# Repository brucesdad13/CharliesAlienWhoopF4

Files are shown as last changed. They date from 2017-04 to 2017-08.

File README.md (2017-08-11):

# UPDATE -- Charlie's AlienWhoop F4 is now OBSOLETE. A new version, deriving from [Lance's AlienFlight F3 Brushed Quad](https://github.com/brucesdad13/AlienFlightArchive/tree/master/Flight-Controllers/F3-V1/F3-Quad), based on the F7 processor has been developed. The AlienWhoop F7 board is backwards compatible, on the same PCB, with F4. The content below has been preserved for historical purposes. Please continue on to [AlienWhoop F7](https://github.com/brucesdad13/AlienWhoopF7)

IMAGE AlienWhoop F4 Flight Controller Welcome

IMAGE AlienWhoop F4 Flight Controller PCB Top Side IMAGE AlienWhoop F4 Flight Controller PCB Bottom Side

# AlienWhoopF4 Features :alien:
AlienFlight F4 remixed for Tiny Whoop/Inductrix

* High-performance ST Microelectronics ARM Cortex-M4 core F4 168 MHz CPU
* Invensense MPU-9250 Nine-Axis (Gyro + Accelerometer + Compass) low power consumption MEMS MotionTracking™ Device
* Latest BetaFlight support (via ALIENFLIGHTF4 target) capable of 32kHz gyro sampling and 16kHz PID loop
* Fairchild Semiconductor FDMA410NZ MOSFET with 9.5A continuous and 24A burst brushed motor insanity (8.5mm coreless scream)

## DIY Flight Controller :alien:
Order your own PCBs from OSH Park by visiting the link below. I recommend ordering the 2oz copper 0.8mm thickness PCB. It takes about three weeks but that will allow plenty of time to order components from the bill of materials in the resources folder. I don't receive any commission or compesation when you order from OSH Park--simply created as a convenience to you (**Note: this version is now obsolete please see the AlienWhoop F7**).
* https://oshpark.com/

## Official Facebook page :alien:
Charlie's AlienWhoop F4 has a Facebook page:
* https://www.facebook.com/alienwhoop/

## See the AlienWhoop F4 in action on YouTube :alien:

IMAGE Soldering the AlienWhoop F4 (https://youtu.be/lKBv_KNc1kM?list=PLFRS68bDc858ymXzT-Lwq0kM343hY3uC5)

IMAGE Charlie's AlienWhoopF4 Takes On Brewmaster's Drone Night 3/25/2017 (https://www.youtube.com/watch?v=Dv2q1gmsQvg)

IMAGE Warm Weather AlienWhoopin' (https://www.youtube.com/watch?v=nY42n2VDJSA)

May this work be of benefit and bring much joy and happiness!

## Acknowledgements :alien:

Deep bows of appreciation and thanks to Lance for his original work and tremendous
generosity in releasing his labor of love for the benefit of all flight controller
enthusiasts. Check out AlienWhoop's heritage at Lance's site:
* http://alienflight.com/ ~ offline as of June 2017
* https://github.com/brucesdad13/AlienFlightArchive ~ Archive of Lance's AlienFlight CC BY-SA suite of flight controllers

Equally deep bows to Jesse Perkins, creator of Tiny Whoop, and the source of inspiration and love for tiny brushed quads.
* http://www.tinywhoop.com/ ~
* https://www.facebook.com/groups/tinywhoop/ ~

Appreciation and respect also goes out to the contributors to the BetaFlight ALIENFLIGHTF4 target including Michael Jakob (MJ666), Martin Budden (martinbudden), and J Blackman (blckmn). Special thanks to Michael Jakob (MJ666) for clearing up confusion on the MPU-9250 magnetometer / compass driver and for updating to MPU-6500 code to work with whichever MPU you decide upon 6500 or 9250 (with compass).

Others deserving thanks for answering questions include in no specific order (and many others):
* OSH Park
* Adam Madron
* Joel Goetze
* Gary Baynes
* Peter (Pedro) Newman

~ Please note: AlienWhoop is not affiliated with nor endorsed by Lance (alienflight.com) or any other Alien projects. The use of Alien in the name and the alien head vector graphic used on the board silkscreen are nods to the lineage of this remix and to the work of Lance and others who created the conditions for this project to arise. Likewise, AlienWhoop is not affiliated with nor endorsed by Tiny Whoop. The Whoop in the name comes from Jesse Perkin's fantastic Tiny Whoop ("a small first-person-view aircraft that truly allows you to feel the gift of flight and the feeling of being tiny" [tinywhoop.com]) and is simply a nod to his efforts and the TW community worldwide.

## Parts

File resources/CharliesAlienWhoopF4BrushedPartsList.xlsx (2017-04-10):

Part | Value | Description | MF | MPN | Mouser | DigiKey | Notes
USB | 10118193-0001LF | Micro-B USB Connector | FCI | 10118193-0001LF | $0.41 |  | Sidemount USB connector
M1 | 53047-0210 | Motor Connector | MOLEX | 53047-0210 | $0.24 |  | Mouser 10 @24 cents
M2 | 53047-0210 | Motor Connector | MOLEX | 53047-0210 | $0.24
M3 | 53047-0210 | Motor Connector | MOLEX | 53047-0210 | $0.24
M4 | 53047-0210 | Motor Connector | MOLEX | 53047-0210 | $0.24
S1 | 2POS-DIP-SWITCH | 2 Position Dip Switch | OMRON | A6H-2102 | $2.55 |  | Substituted for A6H-2101 (backordered)
ACT1 | BLUE | SMD CHIP LED | Kingbright | APHCM2012QBC/D-F01 | $0.21 |  | Mouser 10 @21 cents
ACT2 | BLUE | SMD CHIP LED | Kingbright | APHCM2012QBC/D-F01 | $0.21 |  | IMPORTANT to order BLUE and only BLUE
PWR | BLUE | SMD CHIP LED | Kingbright | APHCM2012QBC/D-F01 | $0.21
R3 | 10K | RESISTORS | Vishay | CRCW060310K0FKEAHP | $0.11 |  | Mouser 10 @11 cents
R4 | 10K | RESISTORS | Vishay | CRCW060310K0FKEAHP | $0.11
R5 | 10K | RESISTORS | Vishay | CRCW060310K0FKEAHP | $0.11
R6 | 10K | RESISTORS | Vishay | CRCW060310K0FKEAHP | $0.11
R7 | 10K | RESISTORS | Vishay | CRCW060310K0FKEAHP | $0.11
R8 | 10K | RESISTORS | Vishay | CRCW060310K0FKEAHP | $0.11
Y1 | 8mhz | SMD Ceramic Resonators | Murata | CSTCE8M00G55-R0 | $0.44
Q1 | FDMA410NZ | N-Channel MOSFET | Fairchild | FDMA410NZ | $0.46 |  | Mouser 10 @46 cents
Q2 | FDMA410NZ | N-Channel MOSFET | Fairchild | FDMA410NZ | $0.46
Q4 | FDMA410NZ | N-Channel MOSFET | Fairchild | FDMA410NZ | $0.46
Q5 | FDMA410NZ | N-Channel MOSFET | Fairchild | FDMA410NZ | $0.46
C4 | 4.7uF | CAPACITORS | Murata | GRJ188C70J475KE11D | $0.16
C7 | 4.7uF | CAPACITORS | Murata | GRJ188C70J475KE11D | $0.16
C10 | .01uF | CAPACITORS | Murata | GRM188R71C103KA01D | $0.03 |  | Mouser 10 @.027 c
C1 | .1uF | CAPACITORS | Murata | GRM188R71C104KA01D | $0.01 |  | Mouser 10 @.01 c
C12 | .1uF | CAPACITORS | Murata | GRM188R71C104KA01D | $0.01
C2 | .1uF | CAPACITORS | Murata | GRM188R71C104KA01D | $0.01
C3 | .1uF | CAPACITORS | Murata | GRM188R71C104KA01D | $0.01
C5 | .1uF | CAPACITORS | Murata | GRM188R71C104KA01D | $0.01
C6 | .1uF | CAPACITORS | Murata | GRM188R71C104KA01D | $0.01
C9 | .1uF | CAPACITORS | Murata | GRM188R71C104KA01D | $0.01
C8 | 1uF | CAPACITORS | Murata | GRM188R71C105KA12D | $0.04 |  | Mouser 10 @.044c
Q3 | IRLML6402 | P-Channel MOSFET | IR | IRLML6402 | $0.38
C11 | 10uF | CAPACITORS | Taiyo Yuden | JMK212AB7106KG-T | $0.22 |  | Mouser 10 @.21c
C13 | 10uF | CAPACITORS | Taiyo Yuden | JMK212AB7106KG-T | $0.22
U1 | MPU9250 | 9-Axis Motion Sensor | Invensense | MPU-9250 |  | $10.64 | Digikey P/N 1428-1019-1-ND
L1 | 2.2uH | 3X3mm Inductor | Taiyo Yuden | NR3015T2R2M | $0.23 |  | Mouser 10 @.23c
MCU | STM32F405RGT | STM32F405RGT | ST | STM32F405RGT |  | $10.58 | Digikey P/N 497-11767-ND
U2 | TPS63001 | Buck/Boost Converter | TI | TPS63001DRCR | $2.25 |  | Mouser 10 @2.02
BAT | JST-PH2.0-PIGTAIL | PowerWhoop Pigtail connector | RDQ | N/A |  | $2.00 | $2 at RaceDayQuads http://bit.ly/2mS2jrU
PCB | PCB | Blade Inductrix shaped PCB | OSH Park | 2oz 0.8mm (http://docs.oshpark.com/services/two-layer-hhdc/) |  | $6.50 | $6.50 for 3 PCB minimum order
RX | LemonRX | LemonRX DSM2 receiver | Lemon | LM0001 (http://www.lemon-rx.com/index.php?route=product/product&path=59&product_id=98) |  | $7.80 | Price seems to have gone up $2.80
Subtotals |  |  |  |  | $11.24 | $37.52
Grand total |  |  |  |  |  | $48.76 | plus shipping the various components
* Recommend directly solder LemonRX. Place face down on bottom side of FC. No JST-ZR_3-PIN connector needed
** Recommend using JST 2.0 pigtail with matching 1S LiPOs >= 200mAh
*** AlienFlight F4 remixed for Tiny Whoop/Inductrix license CC BY-NC-SA 4.0
Optional classic AlienFlight parts: |  |  |  |  |  | DigiKey
REC | JST-ZR_3-PIN | 3 Pin Receiver | JST | S3B-ZR |  | $0.66 | Digikey P/N 455-1694-1-ND
BATT | 3.7V | Battery Connector | JST | S2B-PH-K-S |  | $0.17

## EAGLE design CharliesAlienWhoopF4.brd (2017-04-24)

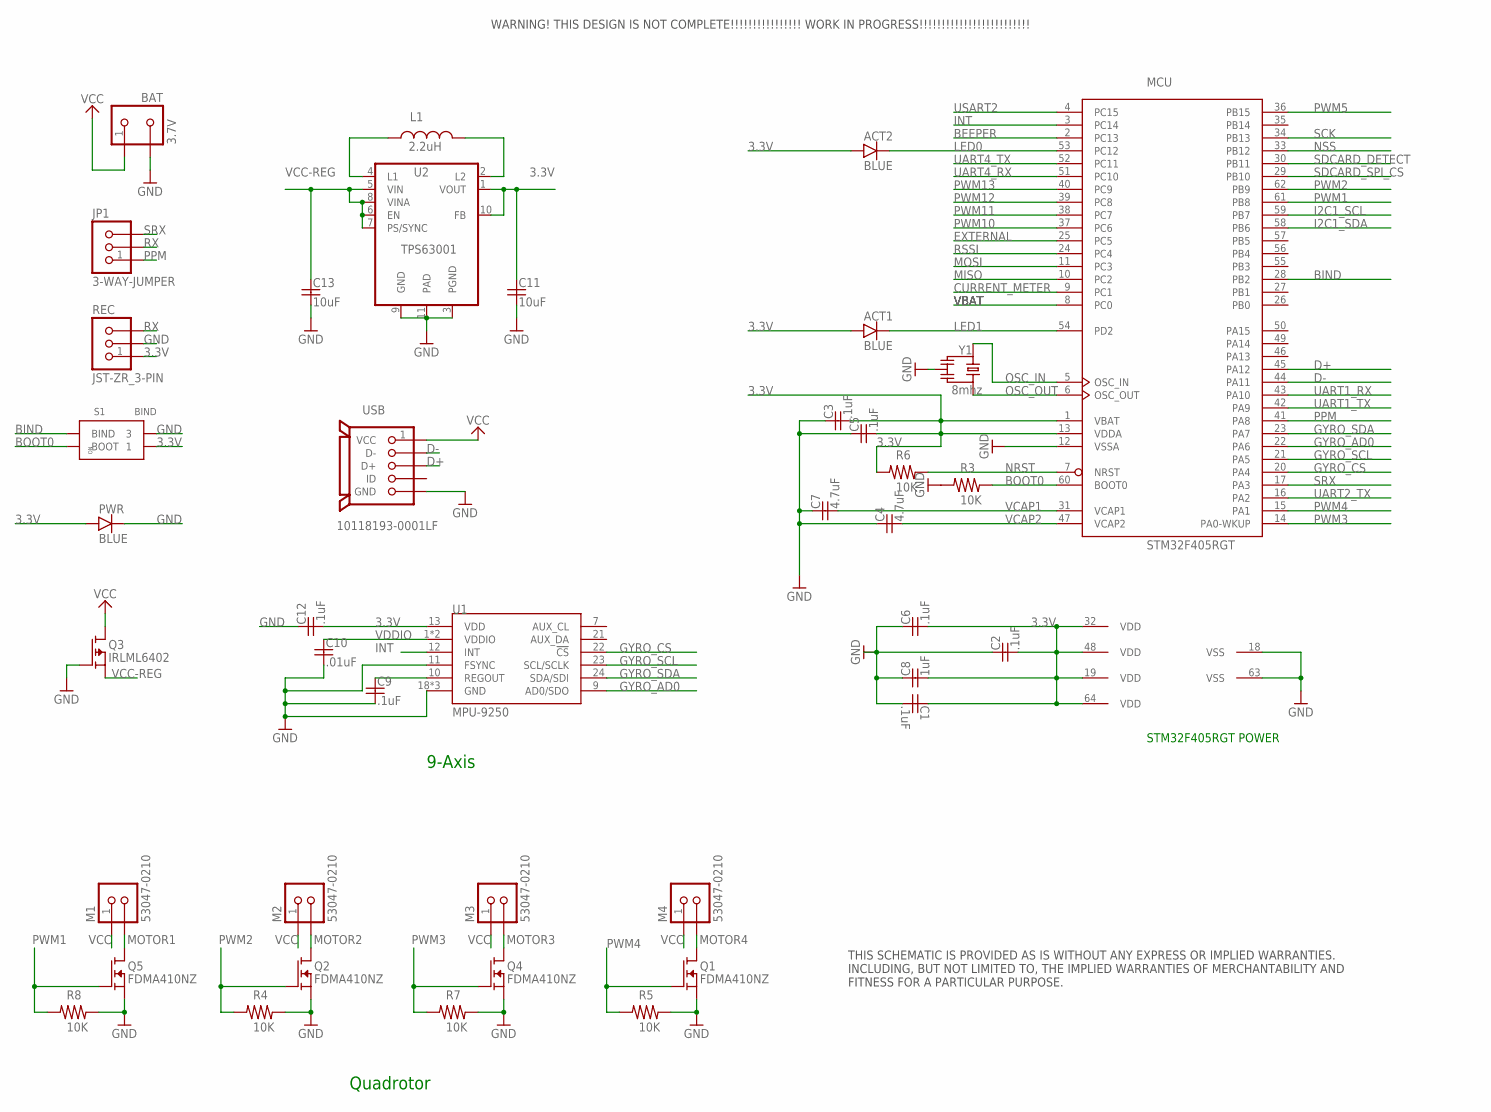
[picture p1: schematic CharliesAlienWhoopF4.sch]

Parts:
ACT1, ACT2: BLUE; SMD-CHIP-LED-0805
BAT: 3.7V; S2B-PH-K-S
C1, C2, C3, C5, C6, C9, C12: .1uF; MUR-CAP-0603
C4, C7: 4.7uF; MUR-CAP-0603
C8: 1uF; MUR-CAP-0603
C10: .01uF; MUR-CAP-0603
C11, C13: 10uF; YUDEN-CAP-0805
JP1: 3-WAY-JUMPER
L1: 2.2uH; NR301X
M1, M2, M3, M4: 53047-0210; PICO-53047-02
MCU: STM32F405RGT; LQFP64
PWR: BLUE; SMD-CHIP-LED-0805
Q1, Q2, Q4, Q5: FDMA410NZ; MICROFET-2X2
Q3: IRLML6402; SOT-23
R3, R4, R5, R6, R7, R8: 10K; VISH-RES-0603
REC: JST-ZR_3-PIN; S3B-ZR
S1: BIND; A6H-2101
U1: MPU-9250; QFN24_PAD
U2: TPS63001; VSON-N10
USB: 10118193-0001LF
Y1: 8mhz; RESONATOR_8

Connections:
3.3V: ACT1.A, ACT2.A, C1.1, C2.2, C3.2, C5.2, C6.2, C8.2, C11.1, C12.2, MCU.1 (VBAT), MCU.13 (VDDA), MCU.19 (VDD), MCU.32 (VDD), MCU.48 (VDD), MCU.64 (VDD), PWR.A, R6.2, REC.1, S1.BOOT_1 (1), U1.13 (VDD), U2.1 (VOUT), U2.10 (FB)
BEEPER: MCU.2 (PC13)
BIND: MCU.28 (PB2), S1.BIND_2 (BIND)
BOOT0: MCU.60 (BOOT0), R3.1, S1.BOOT_2 (BOOT)
CURRENT_METER: MCU.9 (PC1)
D+: MCU.45 (PA12), USB.3 (D+)
D-: MCU.44 (PA11), USB.2 (D-)
EXTERNAL: MCU.25 (PC5)
GND: BAT.2, C1.2, C2.1, C3.1, C4.1, C5.1, C6.1, C7.1, C8.1, C9.2, C10.2, C11.2, C12.1, C13.2, MCU.12 (VSSA), MCU.18 (VSS), MCU.63 (VSS), PWR.C, Q1.S, Q1.S1 (S), Q2.S, Q2.S1 (S), Q3.1 (G), Q4.S, Q4.S1 (S), Q5.S, Q5.S1 (S), R3.2, R4.1, R5.1, R7.1, R8.1, REC.2, S1.BIND_1 (3), U1.11 (FSYNC), U1.18 (GND), U1.20 (GND), U1.CENTER (GND), U2.3 (PGND), U2.9 (GND), U2.11 (PAD), USB.5 (GND), USB.GND, USB.GND2 (GND), USB.HOLE1 (GND), USB.HOLE2 (GND), Y1.2
GYRO_AD0: MCU.22 (PA6), U1.9 (AD0/SDO)
GYRO_CS: MCU.20 (PA4), U1.22 (!CS)
GYRO_SCL: MCU.21 (PA5), U1.23 (SCL/SCLK)
GYRO_SDA: MCU.23 (PA7), U1.24 (SDA/SDI)
I2C1_SCL: MCU.59 (PB7)
I2C1_SDA: MCU.58 (PB6)
INT: MCU.3 (PC14), U1.12 (INT)
L1: L1.1, U2.4 (L1)
L2: L1.2, U2.2 (L2)
LED0: ACT2.C, MCU.53 (PC12)
LED1: ACT1.C, MCU.54 (PD2)
MISO: MCU.10 (PC2)
MOSI: MCU.11 (PC3)
MOTOR1: M1.2, Q5.D, Q5.D1 (D), Q5.D2 (D), Q5.D3 (D), Q5.D4 (D)
MOTOR2: M2.2, Q2.D, Q2.D1 (D), Q2.D2 (D), Q2.D3 (D), Q2.D4 (D)
MOTOR3: M3.2, Q4.D, Q4.D1 (D), Q4.D2 (D), Q4.D3 (D), Q4.D4 (D)
MOTOR4: M4.2, Q1.D, Q1.D1 (D), Q1.D2 (D), Q1.D3 (D), Q1.D4 (D)
NRST: MCU.7 (NRST), R6.1
NSS: MCU.33 (PB12)
OSC_IN: MCU.5 (OSC_IN), Y1.1
OSC_OUT: MCU.6 (OSC_OUT), Y1.3
PPM: JP1.1, MCU.41 (PA8)
PWM1: MCU.61 (PB8), Q5.G, R8.2
PWM2: MCU.62 (PB9), Q2.G, R4.2
PWM3: MCU.14 (PA0-WKUP), Q4.G, R7.2
PWM4: MCU.15 (PA1), Q1.G, R5.2
PWM5: MCU.36 (PB15)
PWM10: MCU.37 (PC6)
PWM11: MCU.38 (PC7)
PWM12: MCU.39 (PC8)
PWM13: MCU.40 (PC9)
REGOUT: C9.1, U1.10 (REGOUT)
RSSI: MCU.24 (PC4)
RX: JP1.2, REC.3
SCK: MCU.34 (PB13)
SDCARD_DETECT: MCU.30 (PB11)
SDCARD_SPI_CS: MCU.29 (PB10)
SRX: JP1.3, MCU.17 (PA3)
UART1_RX: MCU.43 (PA10)
UART1_TX: MCU.42 (PA9)
UART2_TX: MCU.16 (PA2)
UART4_RX: MCU.51 (PC10)
UART4_TX: MCU.52 (PC11)
USART2: MCU.4 (PC15)
VBAT: MCU.8 (PC0)
VCAP1: C7.2, MCU.31 (VCAP1)
VCAP2: C4.2, MCU.47 (VCAP2)
VCC: BAT.1, M1.1, M2.1, M3.1, M4.1, Q3.3 (D), USB.1 (VCC)
VCC-REG: C13.1, Q3.2 (S), U2.5 (VIN), U2.6 (EN), U2.7 (PS/SYNC), U2.8 (VINA)
VDDIO: C10.1, U1.1 (VDDIO), U1.8 (VDDIO)

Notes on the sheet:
THIS SCHEMATIC IS PROVIDED AS IS WITHOUT ANY EXPRESS OR IMPLIED WARRANTIES. INCLUDING, BUT NOT LIMITED TO, THE IMPLIED WARRANTIES OF MERCHANTABILITY AND FITNESS FOR A PARTICULAR PURPOSE.
WARNING! THIS DESIGN IS NOT COMPLETE!!!!!!!!!!!!!!!! WORK IN PROGRESS!!!!!!!!!!!!!!!!!!!!!!!!!
STM32F405RGT POWER
9-Axis
Quadrotor

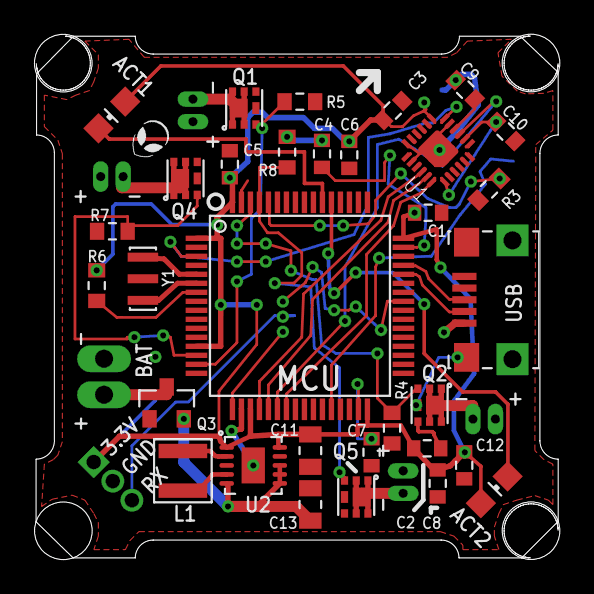
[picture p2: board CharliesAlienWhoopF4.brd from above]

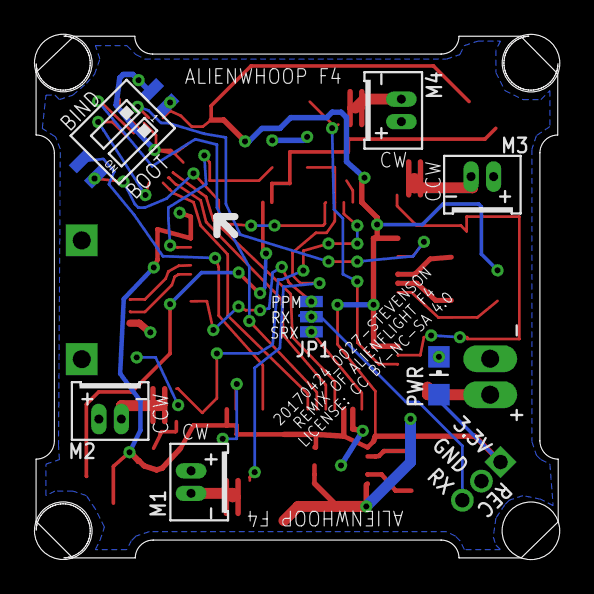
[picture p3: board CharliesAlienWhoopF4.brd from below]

Board: 2 copper layers, 29.0 x 29.0 mm, 41 parts (8 on the bottom side), 35 nets.

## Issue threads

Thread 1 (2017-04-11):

Mounting holes not drilled

brucesdad13, 2017-04-11:
On a recent run from OSH Park the mounting holes portion of the board outline wasn't cut. In correspondence with OSH Park it seems that a better practice is to use a drill at those locations. TODO: update the board with four ~2mm drills at each mounting hole.

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

brucesdad13, 2017-04-24:
Fixed in latest commit (added drill holes and new board outline)

Closed 2017-04-24.

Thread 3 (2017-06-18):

R6 should be 0.1uF capacitor

brucesdad13, 2017-06-18:
Gary Baynes and Michael Jakob of AlienFlight NG have pointed out that the AlienFlight F4 design was based on a misinterpretation of the diagram in the F4 datasheet for the NRST circuit. Rather than requiring an external pullup resistor, the diagram is apparently indicating that the F4 has a builtin permanent pullup resistor. Since the AlienWhoop is a remix of the F4 it inherited this bug.

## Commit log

2017-03-14 Initial import of Eagle project. Cleaning up unused libraries etc.
    [CharliesAlienWhoopF4.brd, CharliesAlienWhoopF4.sch]
2017-03-14 Added a few resources such as the mono bitmap for importing the alien head into silkscreen and a bill of materials/parts list spreadsheetwq
    [CharliesAlienWhoopF4BrushedPartsList.xlsx]
2017-03-16 I was having issues with solder bridges underneath the buckboost. Turns out my traces were too wide and when translated into gerber were leaving not much room for error. Hoping this makes reflow succ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
    [CharliesAlienWhoopF4.brd, CharliesAlienWhoopF4.sch]
2017-03-16 Reduced oscillator traces from 12mil to 11mil. Beginning to rearrange traces for aesthetics... ways to go...
    [CharliesAlienWhoopF4.brd]
2017-03-21 Removed duplicate board outline. Hopefully I got all the line segments. The second run of prototype boards from OSH park it appeared the cut was processed wrong or maybe they just used a larger bit t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
    [CharliesAlienWhoopF4.brd]
2017-03-21 Updated date on silkscreen.
    [CharliesAlienWhoopF4.brd]
2017-03-25 Changed motor orientation back to 1 for my new favorite Furibee frame :)
2017-04-02 Update README.md
    Added link to order PCB
2017-04-02 Added my current betaflight settings for the whoop.
2017-04-04 Update README.md
    Embedded image of the board.
2017-04-08 Updated to remove reference to MPU-6050 and also to note that OMRON 2-position dip switch is sold out and backordered until June on most sites.
    [CharliesAlienWhoopF4BrushedPartsList.xlsx]
2017-04-10 Substituted the sealed version of the OMRON dip switch since the unsealed are backordered until June. Maybe they're trying to reduce inventory?
    [CharliesAlienWhoopF4BrushedPartsList.xlsx]
2017-04-11 Added drill holes to address issue #1
    [CharliesAlienWhoopF4.brd, CharliesAlienWhoopF4.sch]
2017-04-21 Update README.md
    Added special not thanking Michael Jakob for help getting the magnetometer driver situation sorted out.
2017-04-24 Fixed issue #1 mounting holes not drilled/cut. Thanks to advice from OSH Park's Dan Sheadel I'm now using an actual drill command and have redrawn the outline from scratch and am now cutting across t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
    Moved R3 silkscreen label since it was being hidden by a via.
    Ran ERC and DRC etc all passed. -CKS
    [CharliesAlienWhoopF4.brd, CharliesAlienWhoopF4.sch]
2017-04-24 Update README.md
    Updated OSH Park link to latest revision with mounting holes fix.
2017-04-24 Latest settings... subject to change. Might want to reenable notch filters... -CKS
2017-05-20 Added another config with really low motor PWM rate. Loving the results... also dropped the custom mix that turned out to be extraneous thanks to FastEnuf

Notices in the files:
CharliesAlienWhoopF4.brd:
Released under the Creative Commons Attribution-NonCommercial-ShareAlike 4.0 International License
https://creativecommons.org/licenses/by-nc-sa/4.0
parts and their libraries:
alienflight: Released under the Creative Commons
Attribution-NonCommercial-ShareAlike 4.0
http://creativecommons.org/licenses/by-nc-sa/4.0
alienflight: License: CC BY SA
